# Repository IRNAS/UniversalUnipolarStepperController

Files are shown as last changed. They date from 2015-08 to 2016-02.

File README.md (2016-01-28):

# Universal Unipolar Stepper Controller

Here you can find documentation for universal controller for unipolar stepper motors with encoders and end switches.

Check  repository [koruza-instructions](https://github.com/IRNAS/KORUZA-instructions) if you are looking for documentation on how to assemble and use Koruza system. See [project website](http://koruza.net/) for complete specification and introduction.

Should you need any support with KORUZA system, get in touch with Institute IRNAS team and others involved in the project via [chat](https://chat.irnas.eu/) or [forum](http://forum.irnas.eu/).

---

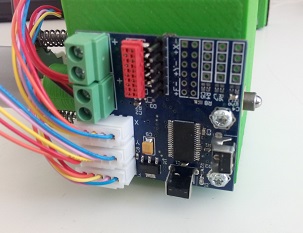
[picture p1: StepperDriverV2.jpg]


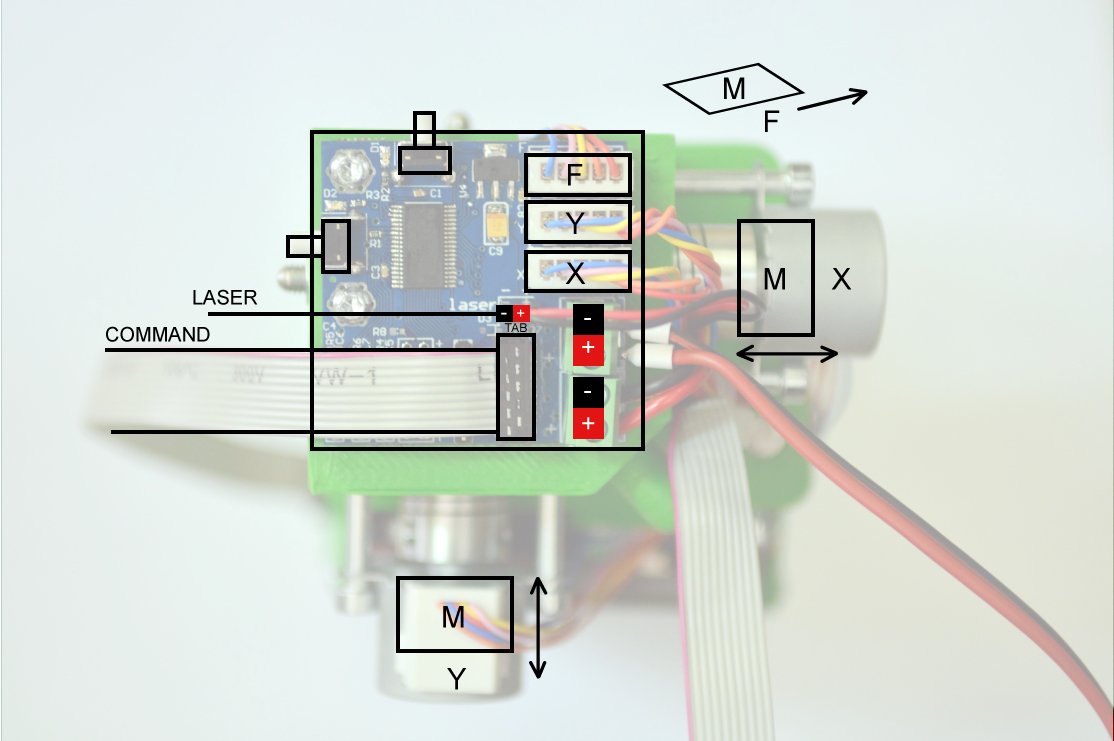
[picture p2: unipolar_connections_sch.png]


The lack of a low-cost stepper controller designed for use with the low-cost motors has motivated us to implement an universal solution with minor optimizations for use in KORUZA. Standalone unipolar motor driver has a number of welcome features:

 * driving 3 unipolar stepper motors 28BYJ48 or 24BYJ48 with suitable JST connectors
 * support for 6 end-switches, two which can be directly attached to the PCB without cables, such that control board can be positioned in a corner of the moving object.
 * support for 3 encoders for closed-loop control in high-precision systems
 * based on Texas Instruments MSP430G2955 in [Energia](http://energia.nu) environment
 * UART, I2C and SPI interfaces for receiving the control commands
 * unified serial connector for all interfaces
 * STATUS: operational prototype
 
Micro-controller has been chosen based on cost and pin number as well as availability in a sufficiently friendly package, however increasing the software development effort. Current revision has been tested with custom Energia code, however we aim to port to it [GRBL](https://github.com/grbl/grbl) firmware and thus make it directly interfacable from computer.

Alternative applications discovered thus-far for the controller board are listed below. We are always looking for ideas and people who would like to use it in their system, do get in touch:

 * 3D printer auto bed-levelling system
 * open-source microscope automation system
 * optics lab micrometer drive motorization
 * mini 3D printers and robots
 
## Firmware

Developed in Energia environment using MSP430G2955 microcontroller not yet officially supported, thus a bit more work in setting up the build environment. Currently only basic functions work and the firmware implemented is here KORUZA specific, but useful for other projects. GRBL port should happen in the future.

### Communicating with the board

UART communication at 115200 baud. Using EasyTransfer you send the whole data structure to the controller and change next values for where you would like the motors to move. Immediately the controller will reply with the data structure filled out with what next position it is moving to and current position where it is at. Positioning is absolute.

---

#### License

All our projects are as usefully open-source as possible.

Hardware including documentation is licensed under [CERN OHL v.1.2. license](http://www.ohwr.org/licenses/cern-ohl/v1.2)

Firmware and software originating from the project is licensed under [GNU GENERAL PUBLIC LICENSE v3](http://www.gnu.org/licenses/gpl-3.0.en.html).

Open data generated by our projects is licensed under [CC0](https://creativecommons.org/publicdomain/zero/1.0/legalcode).

All our websites and additional documentation are licensed under [Creative Commons Attribution-ShareAlike 4 .0 Unported License] (https://creativecommons.org/licenses/by-sa/4.0/legalcode).

What this means is that you can use hardware, firmware, software and documentation without paying a royalty and knowing that you'll be able to use your version forever. You are also free to make changes but if you share these changes then you have to do so on the same conditions that you enjoy.

Koruza, GoodEnoughCNC and IRNAS are all names and marks of Institut IRNAS Rače. 
You may use these names and terms only to attribute the appropriate entity as required by the Open Licences referred to above. You may not use them in any other way and in particular you may not use them to imply endorsement or authorization of any hardware that you design, make or sell.

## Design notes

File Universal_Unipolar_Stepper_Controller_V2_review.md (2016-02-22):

# Universal Unipolar Stepper Controller

Revision of hardware and software for Universal Unipolar Stepper Controller. The main guidelines when considering new design:
- change to ARM microcontroller
- port new software to microcontroller - GRBL
- better power supply for microcontroller and laser, change linear to switching
- measurement of consumption 
- unipolar and bipolar stepper drivers (unipolar is must have)
- board dimension smaller then 50x50 mm
- all current connectors should be on the new board
- native USB on microcontroller and USB connector on board
- developed with open source software
- Arduino or something similar compatible

#### Typical use-cases
- [KORUZA project](http://koruza.net/)
- open-source microscope automation system
- optics lab micrometer drive motorization
- mini 3D printers and robots
- CNC machines, etc.

## 1. Microcontroller (ARM)
Currently there is MSP430G2955 controler on the stepper driver board. This controler costs 3.19 USD, and we want to put cheaper one. Because of the main guidelines from above and new firmware (this will be discussed in Firmware section), microcontroller requirements are:
-  ROM (FLASH) memory must be bigger than 32 KB
-  must have EPROM memory
- at least two ADC for power consumption measurement
- enough GPIOs (~25) for driving stepper drivers, encoders, limit switches 
- communication, etc. 
- UART, SPI, I2C communication
- native USB 
- open source programing environment, Arduino if possible
- unit price smaller then 3 USD

Because of the new firmware, and some additional features like USB and encoders it is good to migrate to new cheaper ARM platform.

## 2. Firmware (GRBL)

Firmware for new revision of Universal Unipolar Stepper Controller will be based on GRBL software. GRBL is software for controlling the motion of machines like CNCs, 3D printers, laser cutters, etc. GRBL is based on Arduino Uno (ATmega328P), but the newer version of software also supports Arduino Mega (ATmega2560). Source code is written in highly optimized C for the ATmega328P microcontroller. They have exhausted almost all its capabilities, and filled the memory (Firmware size is 32 KB). So if we want some new features, new platform is the best solution (ARM). There are projects where people port GRBL firmware to ARM architecture processors, so it is possible. Currently GRBL development team is making new 3D printer and they are writing firmware for ARM, but for now that is all we know. 

GRBL firmware does not support H bridge drivers for driving stepper motors (ULN2003, L295, etc.).

GRBL is good solution for new firmware because it is widely used, professionally written, have good documentation and open source. It should not be a problem to port it to some other architecture and add some new features.

## 3. DC power supply

Current version of the Universal Unipolar Stepper Controller have linear power supply for powering microcontroller and laser (used in KORUZA project). Problem is big heat dissipation because regulator maximum current limit is 800 mA and laser requires about 500 mA to work properly. Additional requirement is that the input voltage should be 24 V, or better 30 V if possible. Output voltage is 3.3 V

Considering all, it is best that new power supply is switching based, because of higher output current, and higher input voltage. That will prevent big heat dissipation.

## 4. Measurement of consumption
All power consumed by the controller must be measured/reported by itself, not accurately, but say in the 20-50 mA accuracy range. There are several ways to measure current consumption, with shunt resistor and op-amp, shunt resistor and two ADCs, special chips working on Hall effect etc.

Because current measurement does not have to be precise, and we already have ADCs in microcontroller, the best and cheapest solution is to put shunt resistor 0.1 Ohm and measure voltages on his ends with two ADCs built in microcontroller. 

## 5. Stepper motor drivers
There are three unipolar stepper motor connectors on current version of the board. New revision of the board must support unipolar stepper motors, and if possible it should support bipolar stepper motors too. Because of the GRBL firmware which does not support drive of H bridges, drivers must be changed. 

Solutions for this are dedicated stepper motor drivers, for unipolar stepper motors. They have two pin interface (direction and step pulse pin), so this will reduce number of pins needed on microcontroller. This drivers also have overcurrent protection and thermal shutdown protection

## 6. PCB and components
Current board dimensions are 45 x 45 mm, and new board should be the same or not bigger than 50 x 50 mm. On the board are connectors:
- 2x power supply
- 1x Universal Serial Connector (UART, SPI, I2C)
- 3x unipolar stepper motor connectors
- 3x encored connectors
- 1x programming/debugging connector
- 1x end switch header connector
- 1x laser connector
and two push buttons on the side. All of this connectors must be on the new version of the board with addition of USB connector. Component package can not be smaller than 0603.
Design rules can be found on this web link: [DESIGN RULES](http://dirtypcbs.com/about.php)

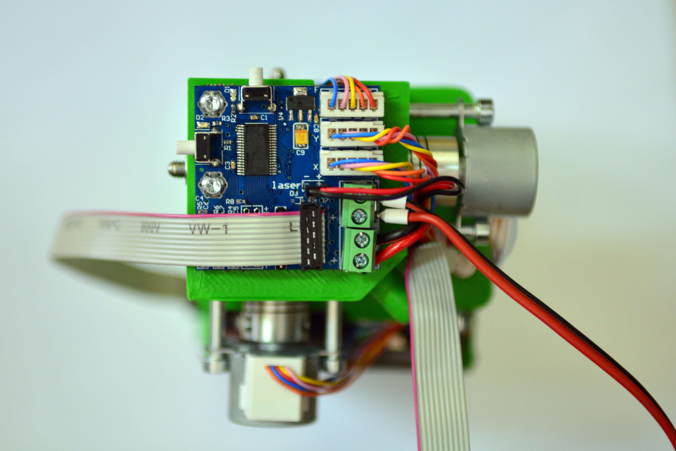
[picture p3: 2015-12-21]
unipolar_connections.jpg

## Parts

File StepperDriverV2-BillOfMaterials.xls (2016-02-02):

Koruza Universal Stepper Driver Bill of Materials
Comment | Description | Designator | Footprint | LibRef | Quantity | Order | Farnell | TME
Capacitor | General capacitor | C1, C2, C3, C4, C5, C6, C7, C8 | 0603 | Capacitor | 8 |  | http://si.farnell.com/multicomp/mc0402f104z160ct/cap-mlcc-y5v-100nf-16v-0402/dp/1758897
TAJB106K020R | Capacitor, Tantalum, 10uF 10% 20V MCCT-B (3528) | C9 | AVX-CAPC3528_V | CMP-0279-00001-1 | 1 |  | http://si.farnell.com/avx/taja106m016r/cap-tant-10uf-16v-case-a/dp/2333010
PowerScrewTerminal |  | Conn1, Conn2 | MKDSN 2,5/ 2-5,08 and powercon | PowerScrewTerminal | 2 |  | http://si.farnell.com/camdenboss/ctb0102-2/terminal-block-wire-to-brd-2pos/dp/2493614
LED | LED diode | D1, D2 | RESC2012X06N | LED | 2 |  | http://si.farnell.com/rohm/sml-310vtt86l/led-smd-0603-red/dp/1685064
3.3V | Diode Zener SMD 3.3V 200mW SOD-323 | D3 | SOD323 | DIODE_ZENER_3V3_SOD323 | 1 |  | http://si.farnell.com/multicomp/bzt55c3v6/diode-zener-0-5w-3-6v/dp/1621862
HEADER-1X4 |  | K1, K2, K3 | HEADER-1X4 | HEADER-1X4 | 3 | one header 40pin breakable needed | http://si.farnell.com/te-connectivity-amp/825433-5/header-1row-5way/dp/1187826
Header 6X2 | Header, 6-Pin, Dual row | K5 | HDR2X6 | Header 6X2 | 1 | one header 40pin breakable needed | http://si.farnell.com/te-connectivity-amp/825433-5/header-1row-5way/dp/1187826
HEADER-1X6 |  | K6 | HEADER-1X6 | HEADER-1X6 | 1 | one header 40pin breakable needed | http://si.farnell.com/te-connectivity-amp/825433-5/header-1row-5way/dp/1187826
Stepper motor connector | Stepper motor 28BYJ48 | M1, M2, M3 | B5B-XH-A | 28BYJ-48 | 3 |  | http://si.farnell.com/jst-japan-solderless-terminals/b5b-xh-a-lf-sn/header-tht-vertical-2-5mm-5way/dp/1516281
Header 2 | Header, 2-Pin | P1 | HDR1X2 | Header 2 | 1 | one header 40pin breakable needed | http://si.farnell.com/te-connectivity-amp/825433-5/header-1row-5way/dp/1187826
 | Micro-Match female PCB connector 10 Positions THT | PoExtension1 | 8-188275-0 | 1-215079-0 | 1 |  | http://si.farnell.com/te-connectivity-amp/8-188275-0/connector-receptacle-smt-1-27mm/dp/3784745
10k | Resistor 0805 smd | R1, R4, R5, R6, R8 | 0603 | Resistor | 5 |  | http://si.farnell.com/multicomp/mc0063w0603510k/res-thick-film-10k-5-0-063w-0603/dp/9331700
1k | Resistor 0805 smd | R2, R3 | 0603 | Resistor | 2 |  | http://si.farnell.com/multicomp/mc0063w060354k7/res-thick-film-4k7-5-0-063w-0603/dp/9332154
/ | Resistor 0805 smd | R7 | 0603 | Resistor | 1 | not installed
SW_THT_ANGLE |  | S1, S2 | TACT_Angle | SW_THT_ANGLE | 2 |  | http://si.farnell.com/te-connectivity/fsmra4jh04/switch-tact-spst/dp/1813692
ULN2003 | Darlington array | U2, U3 | SO-16 narrow | ULN2003 | 2 |  | http://si.farnell.com/texas-instruments/uln2003adr/darlington-array-7npn-2003ade4/dp/1125398RL
LD1117S33TR | Fixed Low Drop Positive Voltage Regulator, 3.3V, 4-Pin SOT-223, Tape and Reel | U4 | SOT-223_L | CMP-0244-00310-1 | 1 |  | http://si.farnell.com/texas-instruments/lm1117mp-3-3/v-reg-ldo-3-3v-1117-sot-223-3/dp/9778195
MSP430G2955 |  | U22 | R-PDSO-G38 | MSP430G2955 | 1 | http://www.digikey.com/product-detail/en/MSP430G2955IDA38R/296-36686-1-ND/4341254 | / | http://www.tme.eu/en/details/msp430g2955ida38r/microcontrollers-others/texas-instruments/

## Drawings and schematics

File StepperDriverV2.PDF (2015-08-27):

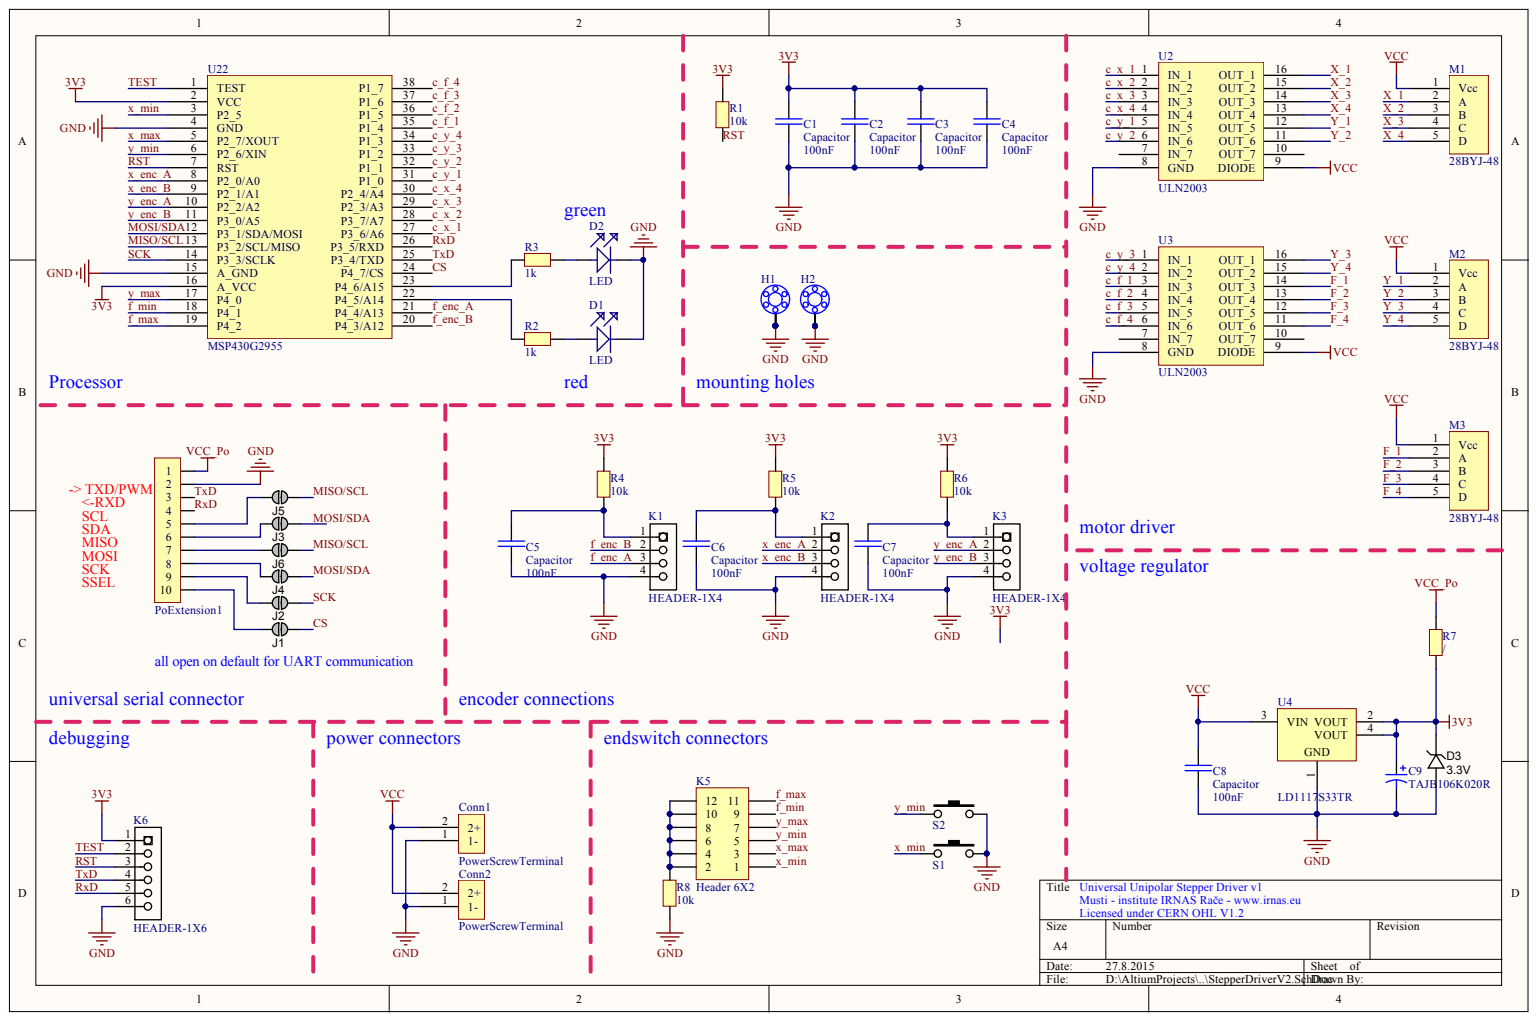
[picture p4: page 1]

-> TXD/PWM <-RXD SCL SDA MISO MOSI SCK SSEL

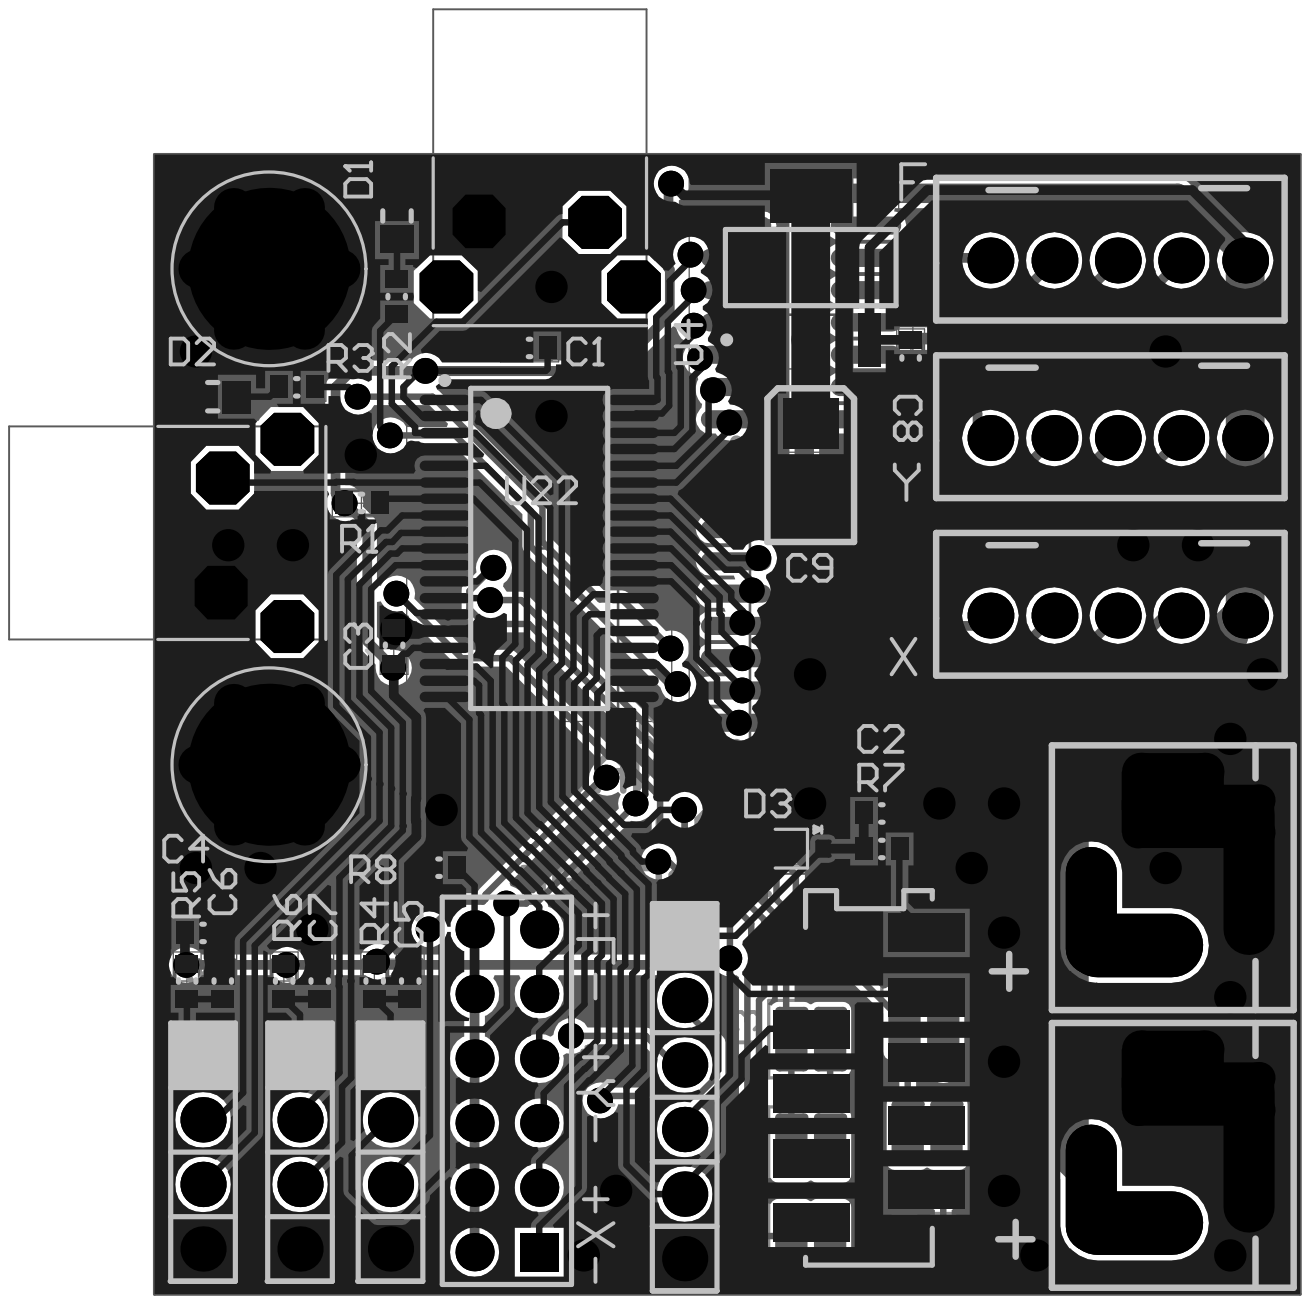
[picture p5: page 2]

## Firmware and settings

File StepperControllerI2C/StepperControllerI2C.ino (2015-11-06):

/* to be used with http://energia.nu/ or http://arduino.cc/
This firmware periodically reads the analog value of the 

Universal Unipolar Sttepper Controller I2C version for use with 28BYJ48 stepper motors

MSP45430G2955 suppored in Energia with modification:
http://forum.43oh.com/topic/3594-msp430g2955-launchpad-development/?p=47184

This support further modified in \energia-0101E0014\hardware\msp430\variants\spir_g2955\pins_energia.h:

*/
// line 106 to: static const uint8_t P2_6 = 29;
// line 377 to: 	P2,  	/* 29 */
// line 421 to: 	BV(6),  	/* 29 */
/*
Copyright Institute IRNAS Rače 2015 - info@irnas.eu

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
You should have received a copy of the GNU General Public License
along with this program.  If not, see <http://www.gnu.org/licenses/>.*/

// http://www.airspayce.com/mikem/arduino/AccelStepper/
#include <AccelStepper.h>

// already in Energia
#include <msp430.h>
#include "MspFlash.h"
#define flash SEGMENT_D
#include <Wire.h>

//serial buffer size has been changed in
//energia-0101E0016\hardware\msp430\cores\msp430

/* Functions implemented:
- move motors to next coordinate specified
- report current coordinate of the motors
- positive and negative endswitches
- limit movement to positive range only
- homing implemented, triggered via command for X and Y simultaneously 
- configuration of speed and acceleration
- 30s after all movement has stopped current location will be stored in flash for reboot persistence
*/

/* Functions implemented:
- encoder support
- general debugging
*/


#define DEBUG
#define PULSEWIDTH 20

//Motors
#define M_X1 P3_6
#define M_X2 P2_3
#define M_X3 P3_7
#define M_X4 P2_4

#define M_Y1 P1_0
#define M_Y2 P1_2
#define M_Y3 P1_1
#define M_Y4 P1_3

#define M_F1 P1_4
#define M_F2 P1_6
#define M_F3 P1_5
#define M_F4 P1_7

#define X_MIN P2_6
#define Y_MIN P2_5
#define F_MIN P4_1

#define X_MAX P4_0// shoudl be 2_7
#define Y_MAX P4_0
#define F_MAX P4_2

#define LED_RED P4_5
#define LED_GREEN P4_6
#define GPIO P4_6

// Creating object for Accel Stepper library
AccelStepper stepperX;
AccelStepper stepperY;
AccelStepper stepperF;

//note distribution of sizes is important for packing
typedef __attribute__ ((packed)) struct struct_motor_t{
  int32_t next_x;
  int32_t next_y;
  int32_t next_f;
  int32_t current_x;
  int32_t current_y;
  int32_t current_f;
  uint8_t status_x; // 24 offset
  uint8_t status_y;
  uint8_t status_f;
  uint8_t empty3;
  uint8_t flash_status;
  uint8_t flash_write_count; 
  uint8_t command; // 30 offset
  uint8_t gpio;
  uint16_t motor_speed;
  uint16_t motor_accel;
};

//Making a union so reading as struct or as char array is possible
union data_t{
 struct_motor_t u;
 unsigned char c[sizeof(struct_motor_t)];
 uint8_t i[sizeof(struct_motor_t)];
};


//Create data structure instance
data_t motor;
data_t motor_rx;

//timing
long timeout_write_flash=0;
long timeout=0;
long timeout_report=0;

boolean write_enable = LOW;

boolean home_enable_x=LOW;
boolean home_enable_y=LOW;
boolean home_enable_f=LOW;
boolean dump_i2c=LOW;

//i2c

char offset=0;

void setup(){
  Wire.begin(4);                // join i2c bus with address #4
  Wire.onReceive(receiveEvent); // register event
  Wire.onRequest(requestEvent);
  Serial.begin(115200);
  Serial.print("Initialized ");
  Serial.println(sizeof(struct_motor_t),DEC);
  // Stepper motors in half step mode, for 24BYJ-48 4000steps per revolution
  stepperX.begin(8,M_X1,M_X2,M_X3,M_X4);
  stepperY.begin(8,M_Y1,M_Y2,M_Y3,M_Y4);
  stepperF.begin(8,M_F1,M_F2,M_F3,M_F4);
  
    // Load current position and the rest from flash
  flash_read();

  if(motor.u.flash_status!=0xab){
    // configure variables
    motor.u.current_x=0;
    motor.u.current_y=0;
    motor.u.current_f=0;
    motor.u.next_x=0;
    motor.u.next_y=0;
    motor.u.next_f=0;
    motor.u.status_x=0;
    motor.u.status_y=0;
    motor.u.status_f=0;
    motor.u.motor_speed=1000;
    motor.u.motor_accel=1000;
    motor.u.command=0;
    motor.u.flash_status=0xab;
    motor.u.flash_write_count=0;
    
    flash_erase();
    flash_write();
  }
  
  flash_read();
 
  // Initialize motors
  stepperX.setCurrentPosition(motor.u.current_x);
  stepperX.setMaxSpeed(motor.u.motor_speed);
  stepperX.setAcceleration(motor.u.motor_accel);
  stepperY.setCurrentPosition(motor.u.current_y);
  stepperY.setMaxSpeed(motor.u.motor_speed);
  stepperY.setAcceleration(motor.u.motor_accel);
  stepperF.setCurrentPosition(motor.u.current_f);
  stepperF.setMaxSpeed(motor.u.motor_speed);
  stepperF.setAcceleration(motor.u.motor_accel);

  // configure endswitches
  pinMode(X_MIN, INPUT_PULLUP);
  pinMode(Y_MIN, INPUT_PULLUP);
  pinMode(F_MIN, INPUT_PULLUP);
  pinMode(X_MAX, INPUT_PULLUP);
  pinMode(Y_MAX, INPUT_PULLUP);
  pinMode(F_MAX, INPUT_PULLUP);
  
  // configure LEDs
  pinMode(LED_RED, OUTPUT);
  digitalWrite(LED_RED, HIGH);
  pinMode(LED_GREEN, OUTPUT);
  digitalWrite(LED_GREEN, LOW);
}

void home_axis(AccelStepper *stepper,long *next,boolean *home_enable, boolean dir, uint8_t status_axis){
  // this function is automatically called once calibration enabled
  // disable homing when not enabled
  if(*home_enable==LOW){
    return;
  }
  
  // 0x1* - minimum reached
  // 0x2* - maximum reached
  
  // evaluate if calibration finished in min
  if(status_axis==0x10 | stepper->currentPosition()==-100000){
    stepper->move(0);
    stepper->setCurrentPosition(0);
    *home_enable=LOW; // disable calibration
    *next=0;
  }
  // evaluate if calibration finished in max
  else if(status_axis==0x20){
    stepper->move(0);
    stepper->setCurrentPosition(100000);
    *home_enable=LOW; // disable calibration
    *next=0;
  }
  else {
    // movement of calibration
    long target=-100000;
    if(dir){
      target*=-1;//move to positive for alignment to positive
    }
    *next=target;
  }
}


// self tests the motors for rotations, such that assembled boards can be checked
void self_test(){
  
  if(motor.u.current_x==0){
    motor.u.next_x=10000;
  }
  if(motor.u.current_x==10000){
    motor.u.next_x=0;
  }
  
  if(motor.u.current_y==0){
    motor.u.next_y=10000;
  }
  if(motor.u.current_y==10000){
    motor.u.next_y=0;
  }
  
  if(motor.u.current_f==0){
    motor.u.next_f=1000;
  }
  if(motor.u.current_f==1000){
    motor.u.next_f=0;
  }
}

// function that executes whenever data is received from master
// this function is registered as an event, see setup()
void receiveEvent(int aCount){
  char data_length=0;
  //first determine the offset through command applies to write and read
  if(aCount > 0){
    offset=Wire.read();
    aCount--; //decrease number of available bytes
  }
  //first determine the offset through command applies to write and read
  if(aCount > 0){
    data_length=Wire.read();
    aCount--; //decrease number of available bytes
  }
  for(char j=0;j<aCount;j++){
    motor_rx.i[offset+j]=Wire.read();
  }
    
  //below is not optimal, further optimization needed
  if(offset==0&data_length>=12){
    // limit movement range to positive
    // shorthand if  condition ? true : false
    motor.u.next_x = motor_rx.u.next_x < 0 ? 0 : motor_rx.u.next_x;
    motor.u.next_y = motor_rx.u.next_y < 0 ? 0 : motor_rx.u.next_y;
    motor.u.next_f = motor_rx.u.next_f < 0 ? 0 : motor_rx.u.next_f;
 }
  if(offset==30){
    //take the command and put it in the reply
    motor.u.command=motor_rx.u.command;
      //run command processing
    process_command();
      //evaluate gpio and write to pin
    boolean gpio_state = motor_rx.u.gpio>0 ? HIGH : LOW;
    motor.u.gpio=motor_rx.u.gpio;
    digitalWrite(GPIO,gpio_state);
  }
}


void requestEvent(){
  if(offset>=sizeof(struct_motor_t)){
    Wire.write(0); //reply null
    //Serial.print(" 0x");
    //Serial.print(1,DEC);
  }
  else{
    Wire.write(motor.c[offset++]); //reply byte and increment offset
    //Serial.print(" 0x");
    //Serial.print(motor_rx.i[offset-1],DEC);
  }
   //Serial.println("");
  //dump_i2c=HIGH;
}


void loop(){
  // enable to test correct board operation
  // self_test();
  
  /*if(dump_i2c){
    dump_i2c=LOW;
    Serial.print(motor.u.current_x);
    Serial.print(" ");
    Serial.print(motor.u.current_y);
    Serial.print(" ");
    Serial.println(motor.u.current_f);
  }*/


  if(timeout_report<millis()){
    //dump_motor_variables();
    timeout_report=millis()+500;
  }

  //update target location of motors
  stepperX.moveTo(motor.u.next_x);
  stepperY.moveTo(motor.u.next_y);
  stepperF.moveTo(motor.u.next_f);
 
  //run motors
  run_motors();
  
  //call homing functiosn, note homing self-disables
  home_axis(&stepperX,&motor.u.next_x,&home_enable_x, LOW, motor.u.status_x);
  home_axis(&stepperY,&motor.u.next_y,&home_enable_y, LOW, motor.u.status_y);
  
  // this should not be needed
  /*motor.u.current_x=stepperX.currentPosition();
  motor.u.current_y=stepperY.currentPosition();
  motor.u.current_f=stepperF.currentPosition();
  */
  
  // automatic store position after idle for a while
  if((timeout_write_flash<millis())&(write_enable==HIGH)){
    flash_erase();
    flash_write();
    write_enable=LOW;
  }
}

void run_motors(){
  //run motors
  //noInterrupts();
  motor.u.status_x=runm(&stepperX,&motor.u.current_x,X_MIN,X_MAX);
  motor.u.status_y=runm(&stepperY,&motor.u.current_y,Y_MIN,Y_MAX);
  motor.u.status_f=runm(&stepperF,&motor.u.current_f,F_MIN,F_MAX);
  //interrupts();
}

void process_command(){
    /*
    1 - stop movement
    2 - home x
    3 - home y
    4 - home f
    5 - configure current position
    6 - configure speed and acceleration
    */
    switch (motor_rx.u.command) {
    case 1: // stop all movement
      stepperX.moveTo(motor.u.current_x);
      stepperY.moveTo(motor.u.current_y);
      stepperF.moveTo(motor.u.current_f);
      home_enable_x=LOW;
      home_enable_y=LOW;
      motor_rx.u.command=0;
      break;
    case 2: // home x
      home_enable_x=HIGH;
      motor_rx.u.command=0;
      break;
    case 3: // home y
      home_enable_y=HIGH;
      motor_rx.u.command=0;
      break;
    case 4: // home f
      motor_rx.u.command=0;
      break;
    case 5: // configure current position
      stepperX.setCurrentPosition(motor_rx.u.next_x);
      stepperY.setCurrentPosition(motor_rx.u.next_y);
      stepperF.setCurrentPosition(motor_rx.u.next_f);
//        //store to flash
//      flash_erase();
//      flash_write();
      motor_rx.u.command=0;
      break;
    case 6: // configure speed and accel
      stepperX.setMaxSpeed(motor_rx.u.motor_speed);
      motor.u.motor_speed=motor_rx.u.motor_speed;
      stepperX.setAcceleration(motor_rx.u.motor_accel);
      motor.u.motor_accel=motor_rx.u.motor_accel;
      stepperY.setMaxSpeed(motor_rx.u.motor_speed);
      stepperY.setAcceleration(motor_rx.u.motor_accel);
      stepperF.setMaxSpeed(motor_rx.u.motor_speed);
      stepperF.setAcceleration(motor_rx.u.motor_accel);
//        //store to flash
//      flash_erase();
//      flash_write();
      motor_rx.u.command=0;
      break;    
    default: 
      // if nothing else matches, do the default
      // default is optional
      break;
  }
}

uint8_t runm(AccelStepper *stepper, int32_t *location, int min_pin, int max_pin){
  // this function runs the stepper motor
  // returns status of limits reached and motion stopped
  // 0x00 - idle
  // 0x01 - moving
  // 0x1* - minimum reached
  // 0x2* - maximum reached
  // 0xff - error
  
  uint8_t return_data = 0x00;
  
  // handle endswitches
  // prevent movement in the direction in which endswitch is pressed
  
  // negative direction endswitch if pin defined
  if(min_pin>0&digitalRead(min_pin)==LOW){
    // stop movement and change return status accordingly
    if(stepper->targetPosition()<stepper->currentPosition()){
      stepper->stop();
      stepper->moveTo(stepper->currentPosition());
      return_data=(return_data|0x10);
    }
  }
  
  // positive direction endswitch
  if(max_pin>0&digitalRead(max_pin)==LOW){
    // stop movement and change return status accordingly
    if(stepper->targetPosition()>stepper->currentPosition()){
      stepper->stop();
      stepper->moveTo(stepper->currentPosition());
      return_data=(return_data|0x20);
    }
  }
  
  // motor movement
  // motor pins are enabled only while moving to conserve power
  if(stepper->currentPosition()!=stepper->targetPosition()){
    stepper->enableOutputs();
    stepper->run();
    // update the current position
    *location=stepper->currentPosition();
    // return moving status
    return_data=(return_data|0x01);
    //reset timeout write for storing position
    timeout_write_flash=millis()+30000;
    write_enable=HIGH;
  }
  // idle
  else{
    stepper->stop();
    stepper->disableOutputs();
    return_data=(return_data|0x00);	
  }
  return return_data;
}

//flash for storing position
void flash_read(){
  Flash.read(flash, motor.c,sizeof(struct_motor_t));
}

void flash_erase(){
  Flash.erase(flash); 
}

void flash_write(){
  motor.u.flash_write_count++;
  Flash.write(flash, motor.c,sizeof(struct_motor_t)); 
}


void dump_motor_variables(){
  Serial.println("");
  Serial.print("Current x: ");
  Serial.println(motor.u.current_x);
  Serial.print("Next x: ");
  Serial.println(motor.u.next_x);
  Serial.print("Status x: 0x");
  Serial.println(motor.u.status_x,HEX);
  Serial.print("Current y: ");
  Serial.println(motor.u.current_y);
  Serial.print("Next y: ");
  Serial.println(motor.u.next_y);
  Serial.print("Status y: 0x");
  Serial.println(motor.u.status_y,HEX);
  Serial.print("Current f: ");
  Serial.println(motor.u.current_f);
  Serial.print("Next f: ");
  Serial.println(motor.u.next_f);
  Serial.print("Status f: ");
  Serial.println(motor.u.status_f);
  Serial.print("Command: ");
  Serial.println(motor.u.command);
  Serial.print("Gpio: ");
  Serial.println(motor.u.gpio);
  Serial.print("Flash write: ");
  Serial.println(motor.u.flash_write_count);
  Serial.print("Accel: ");
  Serial.println(motor.u.motor_accel);
  Serial.print("Speed: ");
  Serial.println(motor.u.motor_speed);
  Serial.print("Home x: ");
  Serial.println(home_enable_x);
  Serial.print("Home y: ");
  Serial.println(home_enable_y);
  
  /*for(char j=0;j<sizeof(struct_motor_t);j++){
    Serial.print(" ");
    Serial.print(motor.c[j],DEC);
  }*/
}

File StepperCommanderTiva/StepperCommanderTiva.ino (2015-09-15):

/* to be used with http://energia.nu/ or http://arduino.cc/
This firmware periodically reads the analog value of the 

UART device communicating with Universal Unipolar Stepper Controller implemented on Tiva C launchpad, adjust UART ports for use with others

MSP45430G2955 suppored in Energia with modification:
http://forum.43oh.com/topic/3594-msp430g2955-launchpad-development/?p=47184

Copyright Institute IRNAS Rače 2015 - info@irnas.eu

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
You should have received a copy of the GNU General Public License
along with this program.  If not, see <http://www.gnu.org/licenses/>.*/

// https://github.com/madsci1016/Arduino-EasyTransfer
#include <EasyTransfer.h>

#define LED PF_2
#define LED_GREEN PF_3

#pragma PACK

//create object
// communication objects
EasyTransfer ETin, ETout; 


struct __attribute__ ((packed)) struct_motor_t{
  int32_t current_x;
  int32_t next_x;
  int32_t current_y;
  int32_t next_y;
  int32_t current_f;
  int32_t next_f;
  uint16_t motor_speed;
  uint16_t motor_accel;
  uint8_t status_x;
  uint8_t status_y;
  uint8_t status_f;
  uint8_t command;
  uint8_t flash_status;
  uint8_t flash_write_count;
  uint8_t gpio;
  uint8_t empty3;
};
// Big warning, struct must be packed for use cross-platform between 8bit, 16bit and 32bit devices

//Making a <union so reading as struct or as char array is possible
typedef union data_t{
 struct_motor_t u;
 char c[sizeof(struct_motor_t)];
 uint8_t i[sizeof(struct_motor_t)];
};

//Create data structure isntance
data_t motor_tx;
data_t motor_rx;


long time_stored;


void setup(){
  Serial.begin(115200);
  Serial.print("Size: ");
   Serial.println(sizeof(motor_rx));
  Serial1.setPins(UART1_PORTB); //trick to active USART1 without overlap USART4
  Serial1.begin(115200);
  //start the library, pass in the data details and the name of the serial port. Can be Serial, Serial1, Serial2, etc.
  ETin.begin(details(motor_rx.c), &Serial1);
  ETout.begin(details(motor_tx.c), &Serial1);
  
  pinMode(LED, OUTPUT);
  digitalWrite(LED, HIGH);
  pinMode(LED_GREEN, OUTPUT);
  digitalWrite(LED_GREEN, HIGH);
  randomSeed(analogRead(0));
  motor_tx.u.command=0;
  time_stored=0;
  motor_rx.u.current_x=1;
  motor_rx.u.current_y=1;
}

char state=0;

void loop(){
  // this test code performs the following operations
  // sets the acceleration and speed
  // moves motors to a position
  // homes X and Y in negative direction
  // creates repeated squares movemenet
  switch (state) {
    case 0:
      motor_tx.u.motor_accel=5000;
      motor_tx.u.motor_speed=300;
      motor_tx.u.command=4;
      state=1;
      break;
    case 1:
      motor_tx.u.next_x=10000;
      motor_tx.u.next_y=10000;
      motor_tx.u.command=0;
      if((motor_rx.u.current_x==10000)&(motor_rx.u.current_y==10000)){
        state=2;
      }
      break;
    case 2:
      //home
      motor_tx.u.command=2;
      if((motor_rx.u.current_x==0)&(motor_rx.u.current_y==0)){
        state=3;
        motor_tx.u.command=0;
      }
      break;
    case 3:
      //move square
      motor_tx.u.next_x=10000;
      motor_tx.u.next_y=10000;
      motor_tx.u.command=0;
      motor_tx.u.gpio=1;
      if((motor_rx.u.current_x==motor_tx.u.next_x)&&(motor_rx.u.current_y==motor_tx.u.next_y)){
        state++;
      }
      break;
    case 4:
      //move square
      motor_tx.u.next_x=20000;
      motor_tx.u.next_y=10000;
      motor_tx.u.command=0;
      if((motor_rx.u.current_x==motor_tx.u.next_x)&&(motor_rx.u.current_y==motor_tx.u.next_y)){
        state++;
      }
      break;
    case 5:
      //move square
      motor_tx.u.next_x=20000;
      motor_tx.u.next_y=20000;
      motor_tx.u.command=0;
      if((motor_rx.u.current_x==motor_tx.u.next_x)&&(motor_rx.u.current_y==motor_tx.u.next_y)){
        state++;
      }
      break;
    case 6:
      //move square
      motor_tx.u.next_x=10000;
      motor_tx.u.next_y=20000;
      motor_tx.u.command=0;
      if((motor_rx.u.current_x==motor_tx.u.next_x)&&(motor_rx.u.current_y==motor_tx.u.next_y)){
        state=3;
      }
      break;
    default:
      // if nothing else matches, do the default
      // default is optional
    break;
  }


/*
  if(motor_rx.u.current_x>45000){
    motor_tx.u.gpio=1;
  }
  else{
    motor_tx.u.gpio=1;
  }
  
  if(motor_rx.u.current_x<5000){
    motor_tx.u.gpio=1;
  }
  else{
    motor_tx.u.gpio=0;
  }

  // here sending some commands for testing each axis
  if(motor_rx.u.current_x==0){
    motor_tx.u.next_x=50000;
    time_stored=millis()+120000;
  }
  else if(motor_rx.u.current_x==50000 & time_stored<millis()){
    motor_tx.u.next_x=0;
  }
  
  if(motor_rx.u.current_y==0){
    motor_tx.u.next_y=50000;
    time_stored=millis()+120000;
  }
  else if(motor_rx.u.current_y==50000 & time_stored<millis()){
    motor_tx.u.next_y=0;
  }
  
  if(motor_rx.u.current_f==0& time_stored<millis()){
    motor_tx.u.next_f=10000;
  }
  else if(motor_rx.u.current_f==10000){
    motor_tx.u.next_f=0;
  }
*/
  //send the data
  digitalWrite(LED, HIGH);
  ETout.sendData();
  digitalWrite(LED, LOW);
  
  //check and see if a data packet has come in. 
  if(ETin.receiveData()){
    digitalWrite(LED_GREEN, HIGH);
    dump_motor_variables();
    //motor_tx.u.command=motor_rx.u.command;//command disables itself
  }
  
  delay(500);
  digitalWrite(LED_GREEN, LOW);
}

void dump_motor_variables(){
  Serial.println("");
  Serial.print("Current x: ");
  Serial.println(motor_rx.u.current_x);
  Serial.print("Next x: ");
  Serial.println(motor_tx.u.next_x);
  Serial.print("Status x: 0x");
  Serial.println(motor_rx.u.status_x,HEX);
  Serial.print("Current y: ");
  Serial.println(motor_rx.u.current_y);
  Serial.print("Next y: ");
  Serial.println(motor_tx.u.next_y);
  Serial.print("Status y: 0x");
  Serial.println(motor_rx.u.status_y,HEX);
  Serial.print("Current f: ");
  Serial.println(motor_rx.u.current_f);
  Serial.print("Next f: ");
  Serial.println(motor_rx.u.next_f);
  Serial.print("Status f: ");
  Serial.println(motor_rx.u.status_f);
  Serial.print("Speed: ");
  Serial.println(motor_rx.u.motor_speed);
  Serial.print("Accel: ");
  Serial.println(motor_rx.u.motor_accel);
  Serial.print("Command: ");
  Serial.println(motor_rx.u.command);
  Serial.print("Command tx: ");
  Serial.println(motor_tx.u.command);
  Serial.print("Flash: ");
  Serial.println(motor_rx.u.flash_status,HEX);
  Serial.print("Flash write count: ");
  Serial.println(motor_rx.u.flash_write_count,DEC);
  Serial.print("State: ");
  Serial.println(state,DEC);
}

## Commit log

2015-09-02 Bug fixes and implemented self-test routine
    [StepperController.ino]
2015-09-15 Added homing and configuration, optimized code
    Siginicant code optimization, added features for homing, full endswitch
    support and introduced a compatible test controller.
2015-11-06 i2c controller
2015-12-21 added schematic for connecting cables
2016-02-02 Added gerbers, Altium source and Bill of materials
    [StepperDriverV2-BillOfMaterials.xls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]

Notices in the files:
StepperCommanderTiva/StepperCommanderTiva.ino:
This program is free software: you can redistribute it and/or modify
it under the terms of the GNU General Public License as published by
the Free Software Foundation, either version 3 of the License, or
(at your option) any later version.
